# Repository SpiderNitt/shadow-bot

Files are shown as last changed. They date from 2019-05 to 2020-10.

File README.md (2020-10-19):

# Shadow-bot
An all-terrain vehicle with an adaptive suspension that is capable of climbing obstacles (walls).

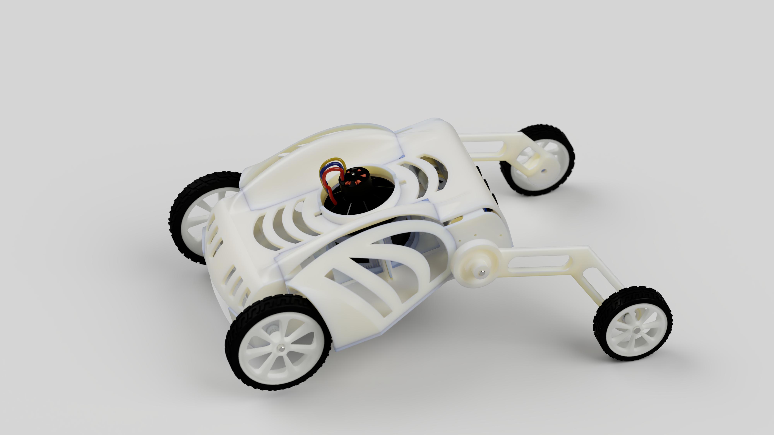
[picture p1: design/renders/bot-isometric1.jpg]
bot


# Research Paper:
[Ibex: A reconfigurable ground vehicle with adaptive terrain navigation capability](https://ieeexplore.ieee.org/document/9196571)

# Team:
  
team

  • Jack Samuel S [https://github.com/jaxxstar] 
  
  • Manu Aatitya [https://github.com/manuaatitya]  
  
  • Senthur Raj [https://github.com/imsenthur]
  
  • Veejay Karthik [https://github.com/vjkarthik97]

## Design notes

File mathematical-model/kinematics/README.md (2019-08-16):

# Longitudinal forward kinematics:

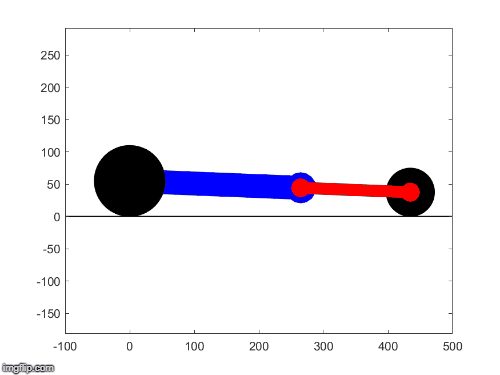
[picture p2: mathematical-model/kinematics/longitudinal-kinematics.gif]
lfk


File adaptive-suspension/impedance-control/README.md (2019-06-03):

# Impedance Control

## Abstract:
The impedance of a mechanical system can be defined as the ratio of the force applied at a point to the resulting velocity at that point. Thus, impedance control is distinct from both position/velocity control and force control. Impedance control is implemented here to achieve the specified desired dynamics.
## Proposed controller
The designed controller is capable of imposing the desired behavior defined by impedance on the original complicated behavior of the end-effector.
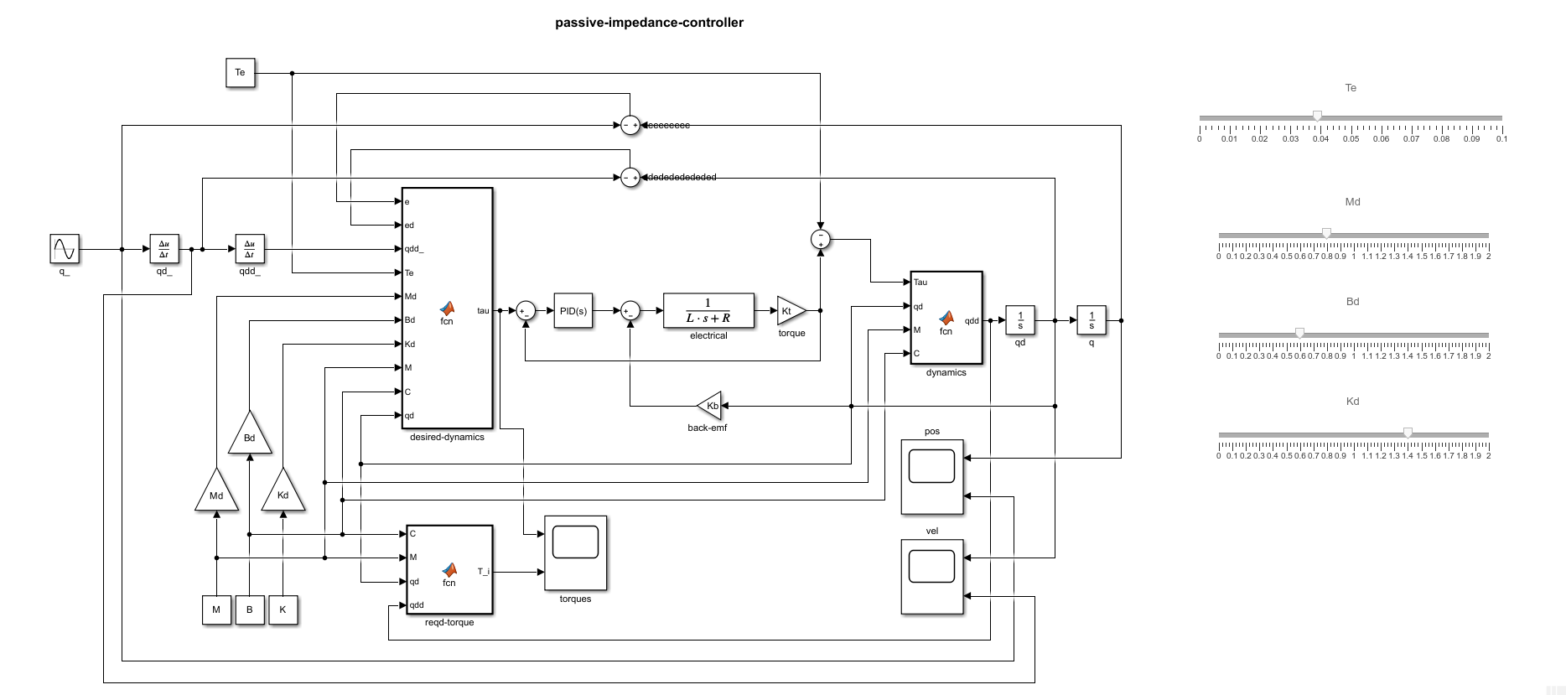
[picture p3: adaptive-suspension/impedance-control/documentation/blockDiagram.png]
Block diagram

## Passivity analysis
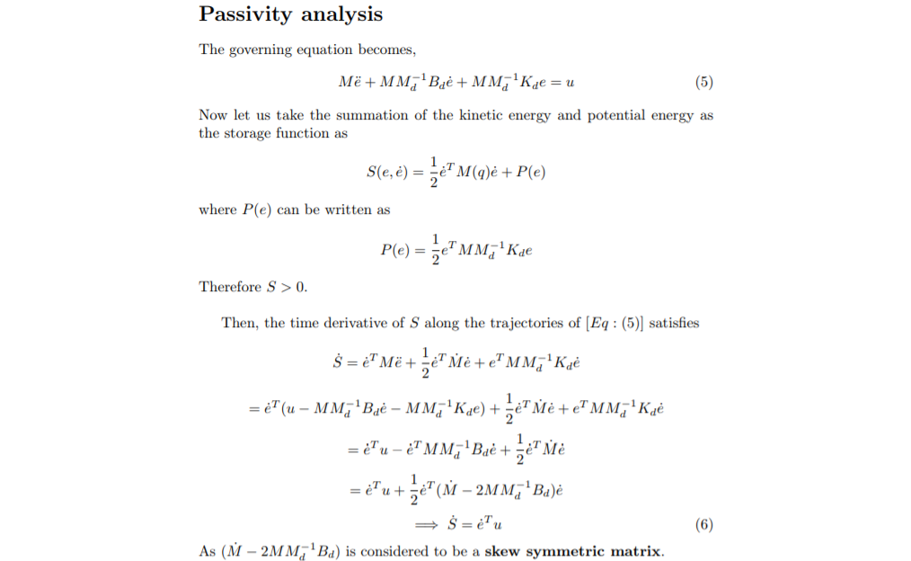
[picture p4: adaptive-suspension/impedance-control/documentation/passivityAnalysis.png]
Passivity analysis

## Modified dynamics
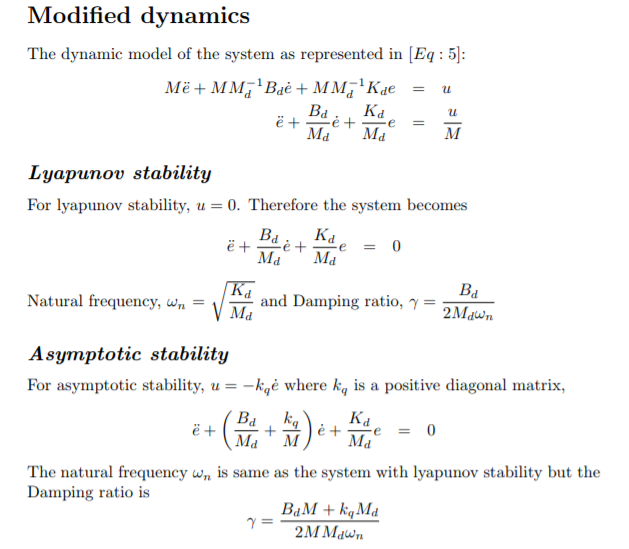
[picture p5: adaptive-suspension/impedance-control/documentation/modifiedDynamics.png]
Modified dynamics

## Results:
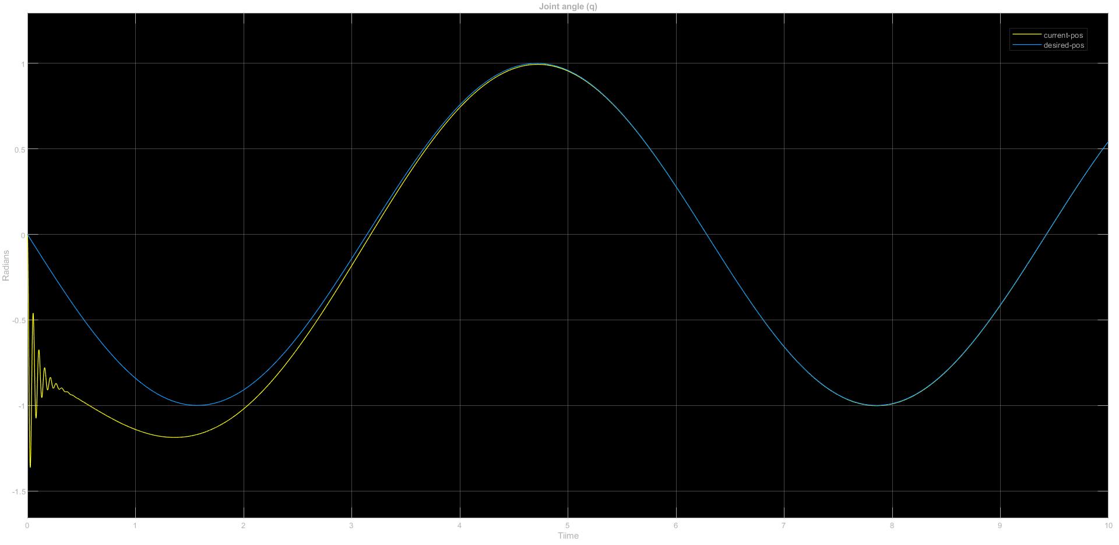
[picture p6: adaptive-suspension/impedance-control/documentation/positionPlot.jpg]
Joint position


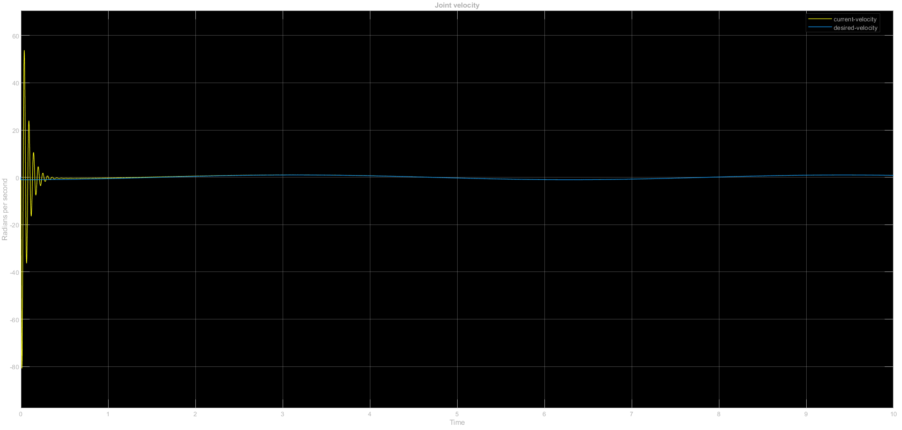
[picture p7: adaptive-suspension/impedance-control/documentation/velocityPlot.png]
Joint velocity


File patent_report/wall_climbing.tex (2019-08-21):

\section{Wall Climbing }
The bot has a unique autonomous wall climbing mechanism which makes it robust to traverse any kind of rough terrain. The wall climbing mechanism is initiated by the response from the ultrasound sensors which detects the presence of obstacles.

The front links then move up and the bot move moves forward. Once the bot reaches the an optimal distance from the obstacle the EDF is turned on to give an upward push and the bot slides along the wall like a ladder. Once the bot is facing the wall the front links are bought down to the original position and the bot moves up on the obstacle due to the EDF Thrust and the rear-wheel drive Torque.

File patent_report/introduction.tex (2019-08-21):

\section{Introduction}

\IEEEPARstart{A}{TR}s  belong to the category of mobile robots which are mainly used for off-road purposes. They usually have wheels or tracks for locomotion. But existing designs have a limitation on the obstacle they can avoid, ie they cannot traverse in a place with really high almost vertical surfaces on all sides. Quite a lot of research has been carried out in the previous decades in this field and excellent ATRs and wall climbing bots have been developed separately.

In the existing Wall climbing bots, an external help is need in order to initially make them fixed to the wall. Several approaches have developed to make the bots move on the walls. Primitive designs use pneumatic suction caps at the end of the actuators to make them fixed on the walls. If the surface is made of ferro-magnetic materials then an electromagnetic actuator is used which gets attached and detached from the surface as the magnet is energized and de-energized. One of the recent bots developed by MIT uses \textit{bio-mimicry} inspired by \textit{Geckos} which have hair like protrusions in order to better grip the surface. But this surface alterations usually involves a cost as nano-materials have to embedded on them. Thus existing bots have a difficulty in commercialization and developed into a product.

Conventional suspensions involve a lot of mechanical components like springs, dampers and struts. The problem with such a system is that a spring has a fixed spring constant and damping constant value arising due to physical structure and material of the spring components. Thus the dynamics of such a system cannot be varied except that a threshold can be set on the maximum load on the spring. Such a spring system cannot be used in an ATR as it encounters new situations depending on the environment it is subjected to. Variable stiffness suspensions are available in the market, but they are expensive and also provide a range of working loads. As loads increase the cost also increase exponentially.

Until recently no bot have been developed with the ability to perform a ground to wall transition autonomously  except \textit{Vertigo}, a bot jointly designed by researchers at \textit{ETH Zurich} and \textit{Disney Research}. Vertigo uses 2 tiltable propellers to maneuver itself in the ground and walls. It has a full carbon fibre frame and servo actuators to rotate the propellers. The carbon fibre frame makes it costly and it also suffers from \textit{gyroscopic precession} which gives a slight jerk whenever the bot tries to change its direction.

The goal of this project is to design an ATR which can be used in any kind of rough terrain with variable size obstacle negotiation capability and dynamic environment adaptability without comprising on the stability at all times. The bot design has been discussed in detail in section II.The Dynamic Analysis, Wall climbing and Adaptive Suspension are discussed in Sections III, IV and V respectively.

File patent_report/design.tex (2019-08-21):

\section{ATR Design}
\begin{figure}
  \begin{center}
  \\
  \caption{Top View of the the proposed design}\label{top_view}
  \end{center}
\end{figure}
The proposed bot design has a set of 2 independently actuated front links who dynamic behaviour can be altered and a set of differential drive rear wheels. Both the rear wheels and the front link positions are actuated using an encoder DC motor. An (Electrically Ducted Fan) EDF is placed in the centre of the bot which provides the necessary thrust during wall climbing to counteract the weight of the bot and provides a kind of drag reduction system during ground motion, aerodynamically aiding the bot's motion in that direction.

%-------------------------------
%   Side View of the bot
%------------------------------

\begin{figure}
  \begin{center}
  \\
  \caption{Side View of the the proposed design}\label{side_view}
  \end{center}
\end{figure}

Slits are cutout from the side of the bot in order to reduce the weight and also to provide an air cooling to the electrical components within the bot. The motors are repeated energizing and de-energizing using an impulse of current in the order of 1 or 2 amperes and over time the current heats the motors due to Joule's Heating Effect and thus needs to be cooled.

Provisions for ultrasound distance sensors and camera are provided in the front of the bot. The cameras help in sensing the environment and relaying the obtained data to a remote location through the on-board WiFi module. The ultrasound sensors help in detecting obstacles, if any, in the advancing direction and the on-board computer sends the appropriate signals to actuate the front links and avoid it.

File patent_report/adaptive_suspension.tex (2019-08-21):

\section{Adaptive Suspension}
Adaptive suspension is one of the key features of shadow bot. The dynamics of the front links can be altered to that of any spring constant and damping constant value thus making it behave as if different springs are being for suspension depending in the load.

Initially the front links are set a desired position. Whenever it encounters an impact the position deviates from the set-point. This change is sensed by the encoders in the motors and error(change in the position) is computed. An impulse of current is sent to the motor which produces a counter torque to balance the impact. Since the frequency of the clock on the on-board CPU is 8MHz, it takes utmost a few milliseconds to react without any delay as electrical components actuate the link whereas in conventional suspensions a lot of delay (on the timescale of electrical actuation) is introduced due to the presence of mechanical and fluid elements in the system.

\begin{figure}[h]
  \begin{center}
  
  \caption{Dynamic behaviour of the link to a varying input}\label{suspesnion_graph}
  \end{center}
\end{figure}

Figure~\ref{suspesnion_graph} shows the response of the link to a varying input. The rise in displacement is the disturbance created from the set position and the fall of displacement is the system's response to the situation. It is observed that the system tries to establish equilibrium is quickier than the time taken to cause the disturbance.

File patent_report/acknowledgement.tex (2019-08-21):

\section*{Acknowledgment}

%Dr. Reveryrand would like to acknowledge the funding by XLIM, Limoges, France. 
We would like to thank the admin, NIT Trichy for providing us a waiver on the 3D printing Cost of the prototype and Siemens COE in Manufacturing, NIT Trichy for 3D Printing the prototy

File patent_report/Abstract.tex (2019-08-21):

\begin{abstract}
%\boldmath

This paper presents the design and dynamical analysis of an All Terrain Robot (ATR) with a novel suspension and wall climbing mechanism. One of the main subsystems of an ATR is the suspension. Traditional suspensions involve spring and dampers with fixed properties which limit the usability of the vehicle. The proposed design uses a rigid front link whose dynamics can be altered according to the impact, thus providing stability in a wide range of environmental conditions. One of the main limitations of the existing all terrain bots is wall climbing. The front links in the proposed design uses a unique wall climbing mechanism to move from the ground to the walls autonomously, which most of the existing design do not address to.

\end{abstract}

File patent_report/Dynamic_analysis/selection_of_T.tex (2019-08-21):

\subsection {Selection of \textbf{T} and \textbf{M_{r}}} 

Consider the bot as shown in Fig.~\ref{top_view}. Let the thrust force provided by the EDF be $\textbf{T}$ \textit{kgf} and the mass of the bot be $\textbf{W}$ \textit{kgf}. When the bot is trying to climb a wall of average coefficient of kinetic friction $\mu$, the following conditions should be satisfied,\\
For No Sliding in the Wall Surface,
\begin{equation}\label{no_sliding}
T \geq \frac{W}{\mu}
\end{equation}

And for No Toppling from the Wall Surface,
\begin{equation}\label{no_toppling}
W \leq T * \frac{x}{c}
\end{equation}
where \textbf{x} is the distance of the EDF centre from the rear wheel of the bot and \\
\textbf{c} is the clearance of the bot with the ground.\\

The required motor torque, \textbf{$M_r$} for the rear wheels to remain in contact with the wall at all times is 
\begin{equation}\label{motor_torque}
M_r \geq \frac{W*R}{2}
\end{equation}
where \textbf{R} is the radius of the wheel.\\

Since we have a range of Thrust, \textbf{T} and Motor torque, \textbf{$M_r$} values to choose from, it must be ensured that the following conditions are always met for the bot to be able to climb on walls,

\begin{equation}\label{thrust_check}
T \geq \frac{W*c - M_r}{x}
\end{equation}

In order to choose the required \textbf{T} and \textbf{W}, the following plots were made :

\begin{figure}[h]
  \begin{center}
  \\
  \caption{T vs W plots for different $\frac{x}{c}$ ratios}\label{TvsW}
  \end{center}
\end{figure}

From Fig.~\ref{TvsW} it is evident that the maximum \textbf{W} that can be lifted for a given value of \textbf{T} is obtained when the EDF is placed at \textit{twice} the clearance of the bot, from the rear end.

\begin{figure}[h]
  \begin{center}
  \\
  \caption{T vs $M_r$ plots for different $\frac{x}{c}$ ratios}\label{TvsTorque}
  \end{center}
\end{figure}

From Fig.~\ref{TvsTorque} it can be inferred that for a given \textbf{T}, \textbf{$M_r$} required to maintain the bot's contact is maximum at \textit{twice} the clearance of the bot, from the rear end.

Thus from the plots it can be concluded that :
\begin{itemize}
    \item There is a trade-off between the payload capacity of the bot and Motor torques for a given amount of Thrust. This can be varied to suit the bot's application, ie for defense applications weight cannot be compromised whereas for inspection in chimneys bot weight can be reduced and thus reducing the cost of the bot.
    \item The $W_{min}$ of the bot that the thrust can support depends on $\mu$ and \textbf{T} only and is independent of other parameters.
    \begin{equation}
        W_{min} = \mu * T
    \end{equation}
\end{itemize}

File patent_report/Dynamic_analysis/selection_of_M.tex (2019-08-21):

\subsection {Selection of \textbf{$M_f$}}

Since front links also share the load of the bot, the minimum torque required to actuate the front links,$M_f$ against the inertial forces must also be analyzed.

\begin{figure}[h]
  \begin{center}
  \\
  \caption{Orientation of the bot in a given state}\label{front_links}
  \end{center}
\end{figure}

Consider a bot orientation as shown in the figure.
Analysing the bot using the method of \textbf{virtual work} to obtain the min Motor torque required we get,\\
Let the distance of the center of mass of the bot from the rear wheels be \textbf{x} and the length of the front links be \textbf{L}.\\
Let's say that the motor produces a torque,$M_f$  to actuate the front wheels,\\
The work done by the motor to rotate the link by an angle $d\theta$ is $M_f * d\theta$.\\
To find Work done by gravity :\\
Using sine rule in the triangle ABC we get,

\begin{equation}\label{sine_rule}
    \frac{sin(\theta}{x} = \frac{sin(\alpha)}{L}
\end{equation}

let the height of the centre of mass of the bot from the ground be \textbf{h},

\begin{equation}
    h = x * sin(\alpha)
\end{equation}

but from equation~\ref{sine_rule}, we get,
\begin{equation}
    x * sin(\alpha) = L * sin(\theta)
\end{equation}
Relating the unknown variables in terms of the known variables using the above equations,  
Work done by gravity for a small displacement $d\theta$ is $-W * x \ *cos(\theta) * d\theta$,\\
the minus sign indicates that the gravity does negative work.\\
Work done by the normal reactions $N_1 \ and \ N_2 \ is \ 0$, since there is not net displacement in the vertical direction.\\
But Frictional force $Fr_{2}$, does some work.\\
let the distance of the front wheel from the point of connection of the front links be y then,\\
$y \ = \ x * cos(\theta)$\\
Work done by frictional force  = $Fr_{2} * x * sin(\theta)*d\theta$\\
Now using work energy theorem we get,\\ $W_{net} \ = \Delta KE_{system}$,
 but since the system is at rest,  
$ KE_{system} \ = \ 0 $
and we get,\\
$ -W * \ x  * \ cos(\theta) * \ d\theta \ + \ Fr_{2} \ * \ x \ * \ sin(\theta)* \ d\theta \ + \ M_{f} * \ d\theta \ = \ 0 $.

Thus $M_{f} \ = W \ * \ x  * \ cos(\theta) * \ d\theta \ - \ Fr_{2} \ * \ x \ * \ sin(\theta)* \ d\theta$,

At $\theta = 0 ^ o$,\\ \\
$M_{f} \ = \frac{W*L*l}{x}$,\\ \\
which is the minimum Motor Torque required for the front links to be actuated.

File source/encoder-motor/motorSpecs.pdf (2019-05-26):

## SPG

## 30 Series

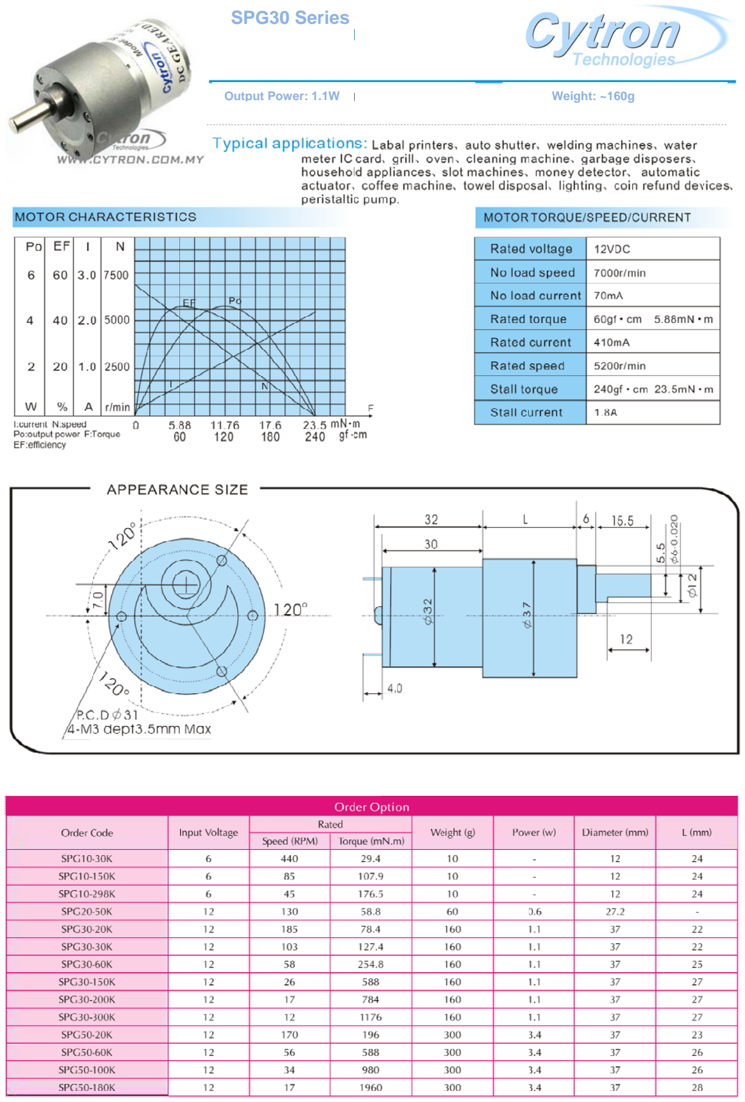
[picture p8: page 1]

Output

Power: 1.1W | Weight: ~160g

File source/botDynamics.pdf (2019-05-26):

## Shadow Bot Calculations

The governing equations are :
Let the Thrust supplied by the EDF be T, and the Weight off the bot be W, then for No Sliding,

and for No Toppling,

where,
x is the point of application of thrust from the rear wheel of the bot, c is the clearance of the bot with the ground.
For the bot to move ,
Motor torque,M required is ,

where,
R = radius of the wheel.

And also the bot should satisfy these conditions while running,

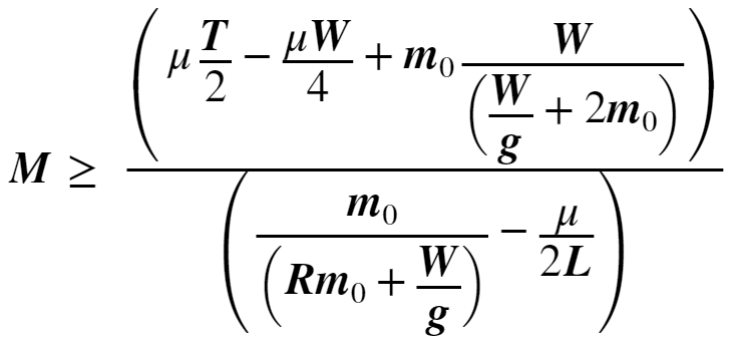
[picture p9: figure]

which has to ensured.
Thrust vs W_max of the bot calculation for different Thrust_distance(x)/clearance of bot ratios keeping other parameters fixed :

% Thrust vs W_max of the bot calculation for different % Thrust_distance(x)/clearance of bot ratios keeping % other parameters fixed
x = table2array(TvsM(13:27,2));
y = table2array(TvsM(13:27,10));
x1 = table2array(TvsM(28:42,2)); y1 = table2array(TvsM(28:42,10)); x2 = table2array(TvsM(43:57,2)); y2 = table2array(TvsM(43:57,10)); x3 = table2array(TvsM(58:72,2)); y3 = table2array(TvsM(58:72,10)); figure;
hold on;
xlabel('Thrust');
ylabel('W-max-toppling');
title('T vs W-max');
plot(x,y,x1,y1,x2,y2,x3,y3);
legend('x/c = 10/8','x/c = 10/7','x/c = 10/6','x/c = 10/5'); grid on;
hold off;

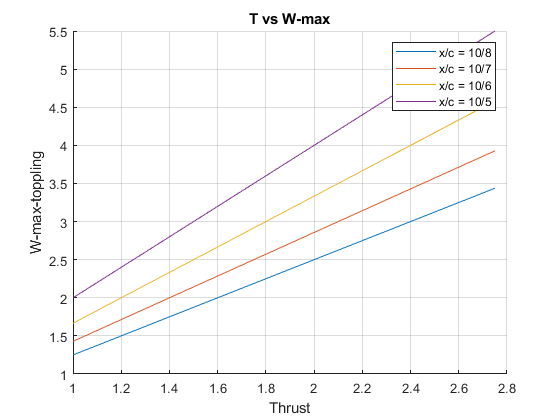
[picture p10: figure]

Motor Torque vs Thrust for the same above conditions :

% Motor Torque vs Thrust for the same above conditions z = table2array(TvsM(13:27,12));

z1 = table2array(TvsM(28:42,12)); z2 = table2array(TvsM(43:57,12)); z3 = table2array(TvsM(58:72,12)); figure;
hold on;
xlabel('Thrust');
ylabel('Motor-Torque-max');
title('T vs Motor-Torque-max'); plot(x,z,x1,z1,x2,z2,x3,z3);
legend('x/c = 10/8','x/c = 10/7','x/c = 10/6','x/c = 10/5'); grid on;
hold off;

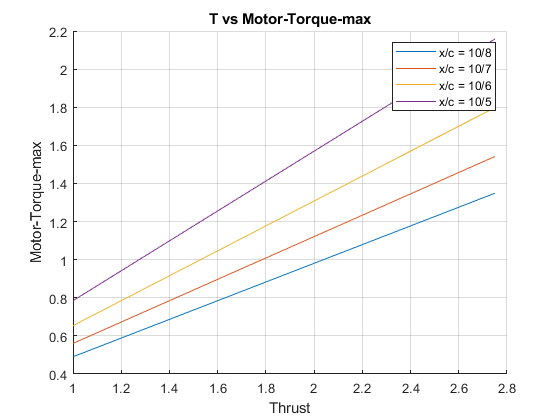
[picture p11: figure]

The Min Motor Torque ,

and | = | and hence depends on µ and T only. It does not depend on other parameters.

Front Wheel Motor Torque:

Calculations for the minimum motor torque required to actuate the front links :

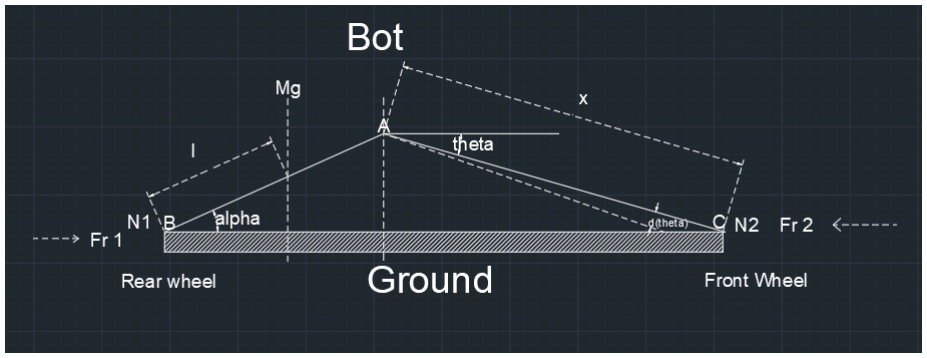
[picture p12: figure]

Analysing the bot using the method of virtual work to obtain the min Motor torque required we get, Le the distance of the center of mass of the bot from the rear wheels be l,
the length of the front links be x.
Let's say that the motor produces a torque, | to actuate the front wheels,
the Work done by the motor to rotate the link by an angle | =

To find Work done by gravity :
Using sine rule in the triangle ABC we get,

let the height of the centre of mass of the bot from the ground be h,

but from (1) we get

but | , where

distance of COM from the back link along the back link

Removing the unknown variable y and relating l and L with the height we get ,

and therefore,

so

Work done by gravity during this time = - | ,

the minus sign indicates that the gravity does negative work.

Work done by the normal reactions | , since there is not net displacement in the vertical direction.

But , frictional force does some work

let the distance of the front wheel from the point of connection of the front links be y then,

Work done by frictional force =

Now using work energy theorem we get ,

Work done by net forces , | but since the system is at rest ,

= 0

and we get ,

- | + ( | ) + | = 0
= | -
and at | we get ,

=

which is the minimum Motor Torque required by the front wheels to be actuated.

Wheel Design :

Euler characteristic ( of Wheel (Disc) is 1.

But,

where,

V is the number of vertices, E is the number of edges,
F is the number of faces.
Let the disc contain P number of Pentagons, H number of Hexagons,
then,

Substituting these values we get,

But we need to find the number of Hexagons,
The number of Hexagons can be arbitrary to fill the remaining space, Here I needded 5 hexagons to cover the fill the disk.
So for our case,

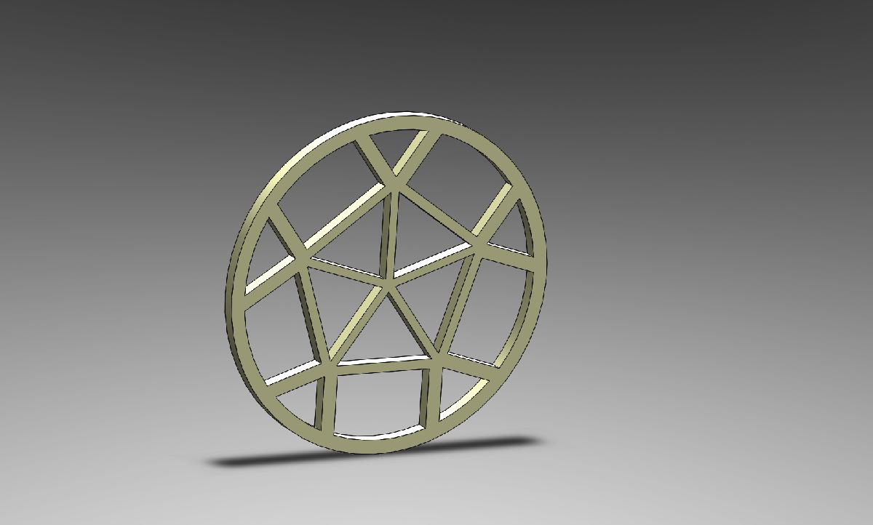
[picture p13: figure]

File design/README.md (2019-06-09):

# Design and development of shadow-bot

## Renders:
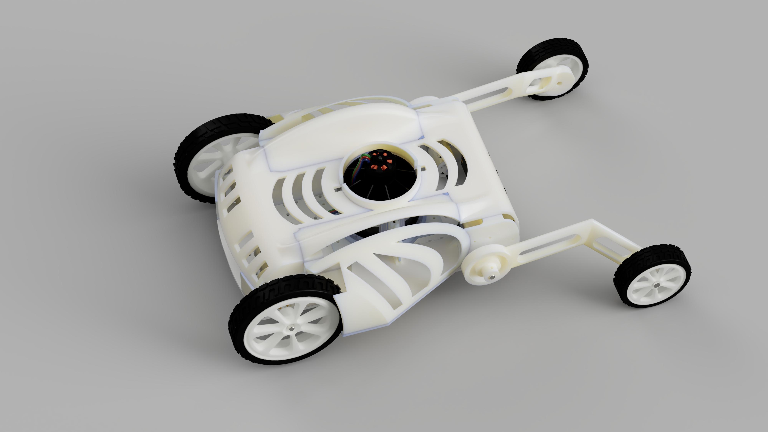
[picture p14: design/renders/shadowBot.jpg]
Passivity analysis


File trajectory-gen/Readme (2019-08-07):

pso1.m - Main Program,run this!!
PSO.m - The Algorithm
conv_splineg1.m - finds and returns the spline characteristics
Sphere.m - The Cost Function

The Trajectory Generated by this is given to the controller as a the reference to be followed.

In this problem we try to generate trajectories based on cubic
splines.The cubic splines require a set of waypoints and a set of time
stamps during which they have to be traversed through.The waypoints are
generated from path planning algorithms and the time stamps are to
determined based on the physical limitations of acceleration and
velocities of our bot.This trajectory generation aims to generate a set of optimal time intervals which 
helps us to construct the required cubic
spline.Since the optimization problem here is highly non convex and non
linear in case of cubic splines,we employ a method called particle swarm optimization to help us
achieve our objective.

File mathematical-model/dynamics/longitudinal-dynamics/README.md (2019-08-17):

# Longitudinal Dynamics:

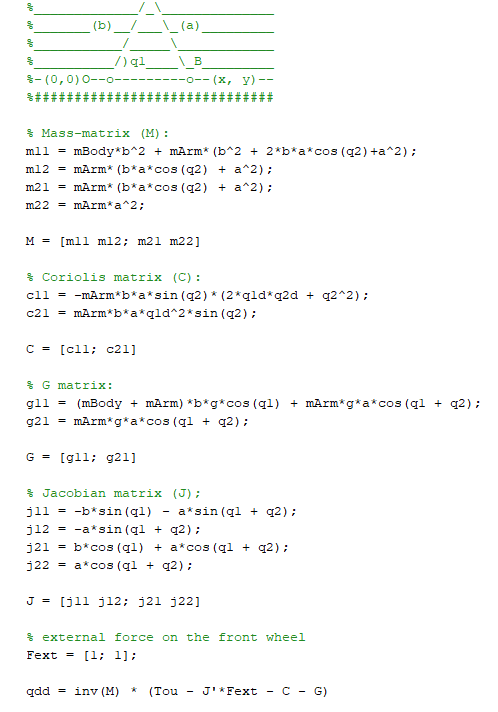
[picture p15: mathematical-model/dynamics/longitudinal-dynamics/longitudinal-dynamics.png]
LD


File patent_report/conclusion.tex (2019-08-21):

\section{Conclusion}
In summary, this report discusses about :
\begin{itemize}
    \item ATRs and wall climbing bots, the existing designs and limitations,
    \item How the proposed design overcomes the limitations presented by the existing bots, without compromising the performance,
    \item How adaptive suspension is superior to the current technologies for suspensions in ATRs or All Terrain Vehicles in general,
    \item How the integration of the suspension and wall climbing modules makes the bot traverse through any terrain with ease and
    \item How the cost of maintenance and repair in conventional ATRs can be reduced by introducing the proposed modules.
\end{itemize}

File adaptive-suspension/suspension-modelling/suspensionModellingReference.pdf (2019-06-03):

Modelling:

Models can be based on equation, data.

Different types of modelling using Simulink:

i) Mathematical Models (Writing equations)

1.First Principles

2.Component-based physical models

ii) Black Box Models (Solely based on input and output data)

1.Lookup Tables

2.System Identification *(Dynamically changing functions using curve fitting)

iii)Grey Box Models (We know some eqns. but not sure about the parameters so we write eqns. and collect data so that the data can be used to tune the parameters)

1.Parameter estimation*

*Powerful tools

Models can be generally divided into 2 parts:

i) Plant Model- Virtual Prototype of a real physical System and these systems can be modelled with the help of data collected from the real system (or) getting the mathematical equation from physics

ii) Algorithm- Control and Logic systems, Design in Simulink and then generate code for the embedded system

Simulink helps us to combine these 2 parts

Suspension System of Cars:

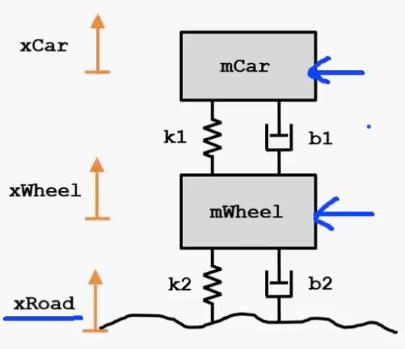
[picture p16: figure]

There is assumed to be one extra set of spring and damper one between the wheel and the road and the other which is physically present

This is done in real cars because to account for the wheel squishing against the road, but we can choose to neglect this in shadow bot

## Mathematical Modelling of Car suspension:

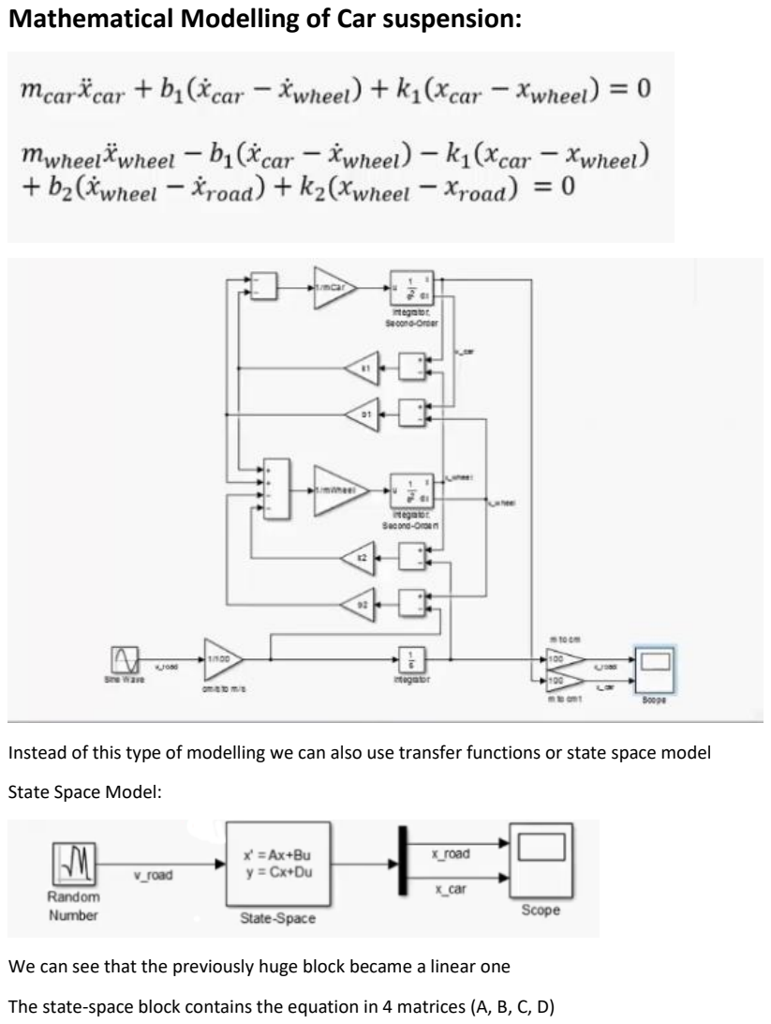
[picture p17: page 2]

Instead of this type of modelling we can also use transfer functions or state space model

State Space Model:

We can see that the previously huge block became a linear one

The state-space block contains the equation in 4 matrices (A, B, C, D)

Component Based Modelling (Simscape):

Simscape a tool for physical modelling which has blocks which has the equations inside it i.e. we don’t need to know the equations and if there are any changes in the system then we don’t need to re formulate the eqns. again from scratch we can just alter the blocks

Both Simulink and Simscape are compatible i.e. we can integrate plant model in Simscape and control in Simulink with the help of interface blocks

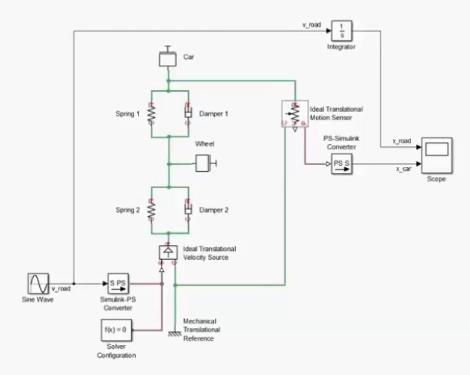
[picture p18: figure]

Black Box Approach:

We have this data:

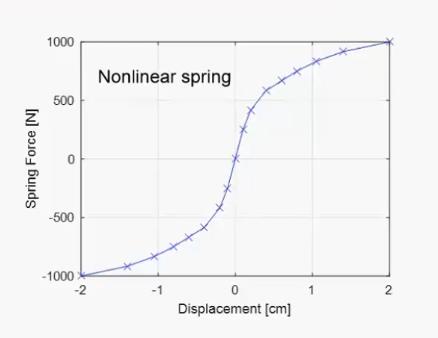
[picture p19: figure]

We can import data from excel sheets or text file

We simply insert a block stating the parameters from the file which has the plots

Parameter Estimation:

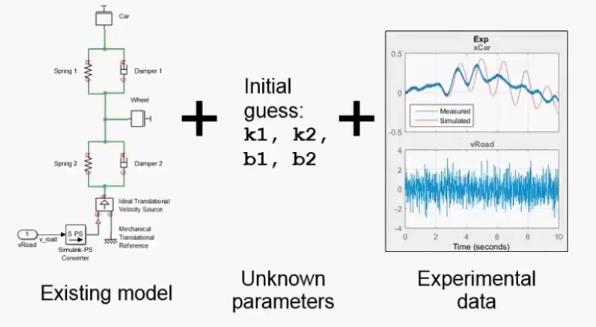
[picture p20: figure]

In this method if it takes too long for the computer to iterate and simulate the data we could something called as parallel computing &|| GPU computing which would be really cool.

Here the parameters are given an initial guess and MATLAB iterates the simulation many number of times to get an optimised value for those parameters (We will have to read about optimisation theory)

System Identification:

This type of modelling is done when we don’t know anything about the system except for input and output data

Here we could really play around with MATLAB and write different Model structures such as state space/ transfer function/ Non-linear model, but for a particular system a particular model structure will work flawlessly, so we’ll have to decide which structure we are going to use in case we are going to use system identification modelling.

To get the best model structure we start with the simpler linear model (State Space) and if it does not work fine then we go to transfer function or non-linear structure

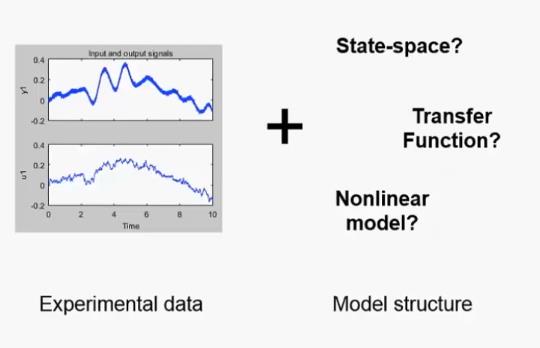
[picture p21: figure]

System Identification by state space approach:

By using state space model, we could know the different states of the system at any instant

Here we specify the order of the system, i.e. the number of system variables

Guidelines for choosing from the different model approach

1.How much we know about the model (Physics of the model)

If we know everything then we could use the mathematical approach in which the model will be the most accurate to real world, but In case we don’t know anything about the model it is okay to use system identification approach

2.How much detail we want from the model.

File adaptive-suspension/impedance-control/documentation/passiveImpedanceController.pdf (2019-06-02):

# Impedance controller and design of desired parameters

Senthur Raj

May 30, 2019

## Introduction

This report describes the way of approach, the progress and the results obtained. The research objective is to find a novel way to design the impedance parameters (Md, Bd and Kd) with the help of passivity analysis.

## Passivity

Let us consider a system H with input u(t) and output y(t), where H is regarded as a mapping from input space to output space. Then, passivity of the map can be defined as [1],
The system H : u =⇒ y is said to be passive if there exists a positive constant β such that,
Z τ

0

y

T
(t)u(t)dt ≥ −β

for all input signals u(t) and for all τ ∈ R⁺. In addition, H is said to be

- Input strictly passive if there exists a positive scalar δu such that
Z τ

0

y

T
(t)u(t)dt ≥ −β + δu

Z τ

0

||u(t)||²
dt,
- Output strictly passive if there exists a positive scalar δy such that
Z τ

0

y

T
(t)u(t)dt ≥ −β + δy

Z τ

0

||y(t)||²
dt,

For example, let us consider a n-link manipulator, the robot dynamics can be written as
M(q)¨q + C(q, q˙) ˙q + G(q) = T | (1)

1

where q, ˙q and ¨q represent joint angles, velocities, and accelerations respectively, and T represents the input torque vector. The matrices M(q) and C(q, q˙) represent the manipulator inertia matrix and Coriolis matrix respectively and the gravity vector G(q) can be written as

G(q) =
∂P(q)

∂q T

where P(q) is potential energy of the system.
It is well known that M(q) is positive definite and the matrix

M˙
(q) − 2C(q, q˙)

is skew-symmetric by defining C(q, q˙) using the Christoffel symbols.
Let us take the summation of the kinetic energy and potential energy as the storage function as
S(q, q˙) = 1
2

q˙

TM(q) ˙q + P(q)

Then, the time derivative of S along the trajectories of Eq : (1) satisfies

S˙ = ˙q
TM(q)¨q +
1/2 q˙

TM˙
(q) ˙q +
∂P (q)

∂q
q˙

= ˙q

T

(T − C(q, q˙ − G(q)) + 1
2

q˙

TM˙
(q) ˙q + G(q)

T
q˙)

= ˙q

T T −
1/2 q˙

T

(M˙
(q) − 2C(q, q˙)) ˙q

=⇒ S˙ = ˙q
T T

The last equation holds because of the skew symmetry of M˙
(q)−2C(q, q˙). This
means passivity of the manipulator dynamics from the input torque T to the joint velocity ˙q.

## Impedance control

The designed controller is capable of imposing the desired behavior defined by impedance on the original complicated behavior of the end-effector [2]. The actual dynamic model of a 5-bar manipulator can be expressed as

M(q)¨q + C(q, q˙) ˙q + G(q) = Tinp − Text | (2)

The desired impedance model according to the specific work requirements which is usually specified as a second-order dynamic equation:

Mdë+ Bde˙ + Kde = −Text | (3)

where e = (q − qd).

2

After substituting the target impedance [Eq : 3] into the actual manipulator dynamics [Eq : 2] by eliminating ¨q, a specific control law is obtained as

Tinp = u+(1+MM⁻¹
d

)Text+C(q, q˙) ˙q+G(q)+M(q)[ ¨qd−M⁻¹
d

[Bde˙+Kde+Text]]
(4)
since
q¨ = ¨qd − M⁻¹
d

[Bde˙ + kde + Text]

The control law [Eq : 4] is the desired one to make the actuators produce torque Tinp. Then the manipulator driven by Tinp will perform the behavior defined by impedance in [Eq : 3].

## Passivity analysis

The governing equation becomes,

Më+ MM⁻¹

d | Bde˙ + MM⁻¹
d | Kde = u | (5)

Now let us take the summation of the kinetic energy and potential energy as the storage function as

S(e, e˙) = 1
2

e˙

TM(q) ė + P(e)

where P(e) can be written as

P(e) = 1
2

e

TMM⁻¹
d Kde

Therefore S > 0.

Then, the time derivative of S along the trajectories of [Eq : (5)] satisfies

S˙ = ė
TMë+

1
2

e˙

TM˙ e˙ + e

TMM⁻¹
d Kde˙

= ė

T

(u − MM⁻¹

d | Bde˙ − MM⁻¹
d | Kde) + 1
2 | e˙ TM˙ e˙ + e

TMM⁻¹
d Kde˙

= ė

T u − e˙

TMM⁻¹
d | Bde˙ +
| 1
| 2 e˙ TM˙ e˙

= ė

T u +

1
2

e˙

T

(M˙ − 2MM⁻¹
d Bd) ė

=⇒ S˙ = ė
T u | | (6)

As (M˙ − 2MM⁻¹
d Bd) is considered to be a skew symmetric matrix. [Eq : 6] implies that the system [Eq : 5] is passive from input u to output e˙. Also notice that the storage function is shaped so that it takes the minimal value at e = 0 and ė = 0.

3

Substituting ė = 0 and u = 0 in [Eq : (5)], we get

e = 0

and hence the system is zero-state observable and lyapunov stable. Thus, the damping injection
u = −kqe˙ | (7)

If kq is a diagonal positive gain matrix, then it guarantees
asymptotic stability of the origin ė = 0 and e = 0.

## Modified dynamics

The dynamic model of the system as represented in [Eq : 5]:

Më+ MM⁻¹

d | Bde˙ + MM⁻¹
d | Kde = u

ë+

Bd
Md

e˙ +

Kd
Md

e =

u
M

Lyapunov stability

For lyapunov stability, u = 0. Therefore the system becomes

ë+

Bd
Md

e˙ +

Kd
Md

e = 0

Natural frequency, ωn =

r
Kd
Md

and Damping ratio, γ =

Bd
2Mdωn

Asymptotic stability

For asymptotic stability, u = −kqe˙ where kq is a positive diagonal matrix,

ë+

Bd
Md

+

kq
M
e˙ +

Kd
Md

e = 0

The natural frequency ωn is same as the system with lyapunov stability but the Damping ratio is

γ =

BdM + kqMd
2MMdωn

## References

[1] Takeshi Hatanaka, Nikhil Chopra, Masayuki Fujita, and M.W. Spong. Passivity-Based Control and Estimation in Networked Robotics. 01 2015.
[2] P. Song, Y. Yu, and X. Zhang. Impedance control of robots: An overview. In 2017 2nd International Conference on Cybernetics, Robotics and Control (CRC), pages 51–55, July 2017.

4

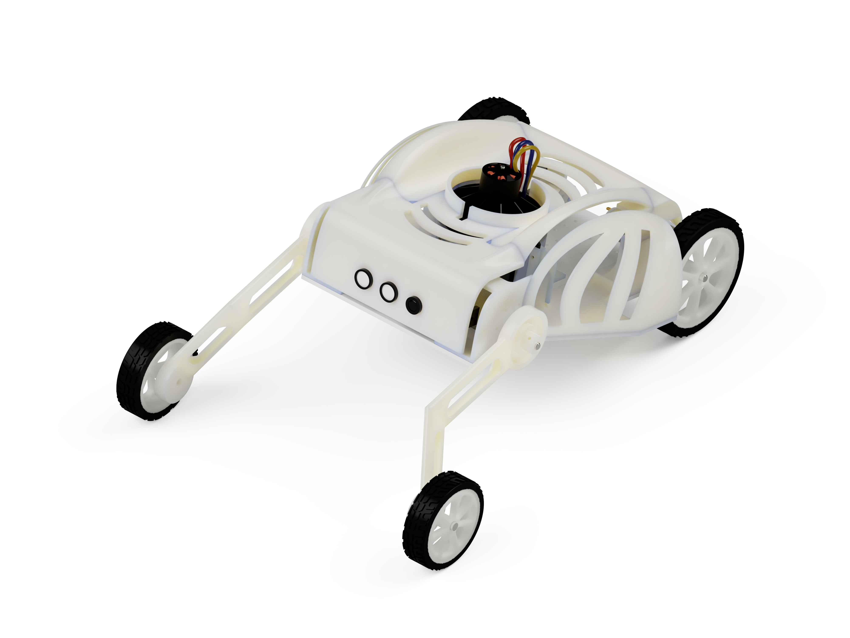
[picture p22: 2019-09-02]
design/renders/ICRA/isometric.PNG

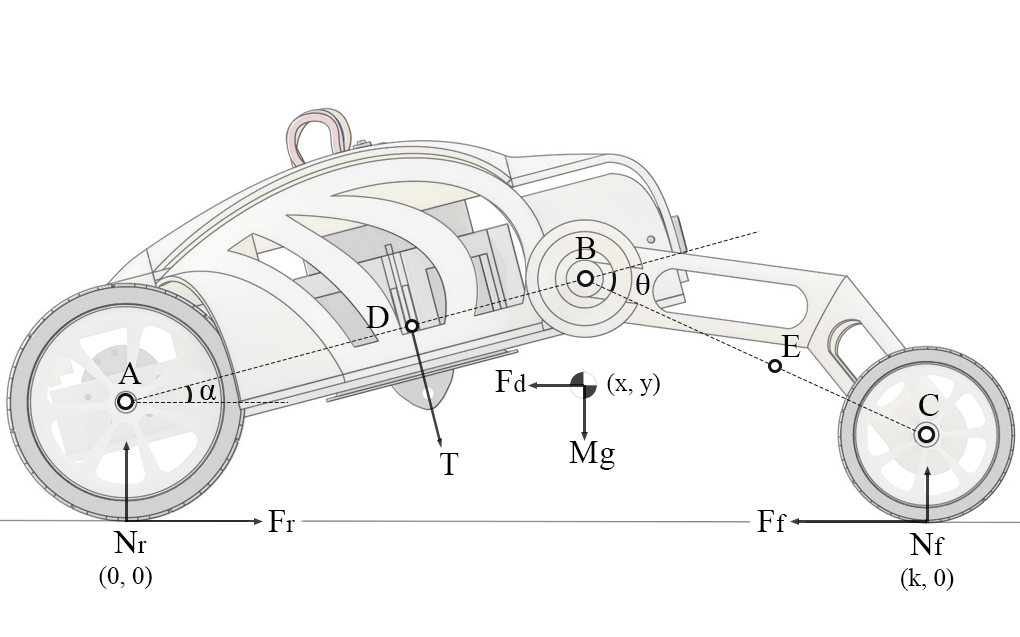
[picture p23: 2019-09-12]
design/renders/ICRA/fbd-kinematics-fusion.png

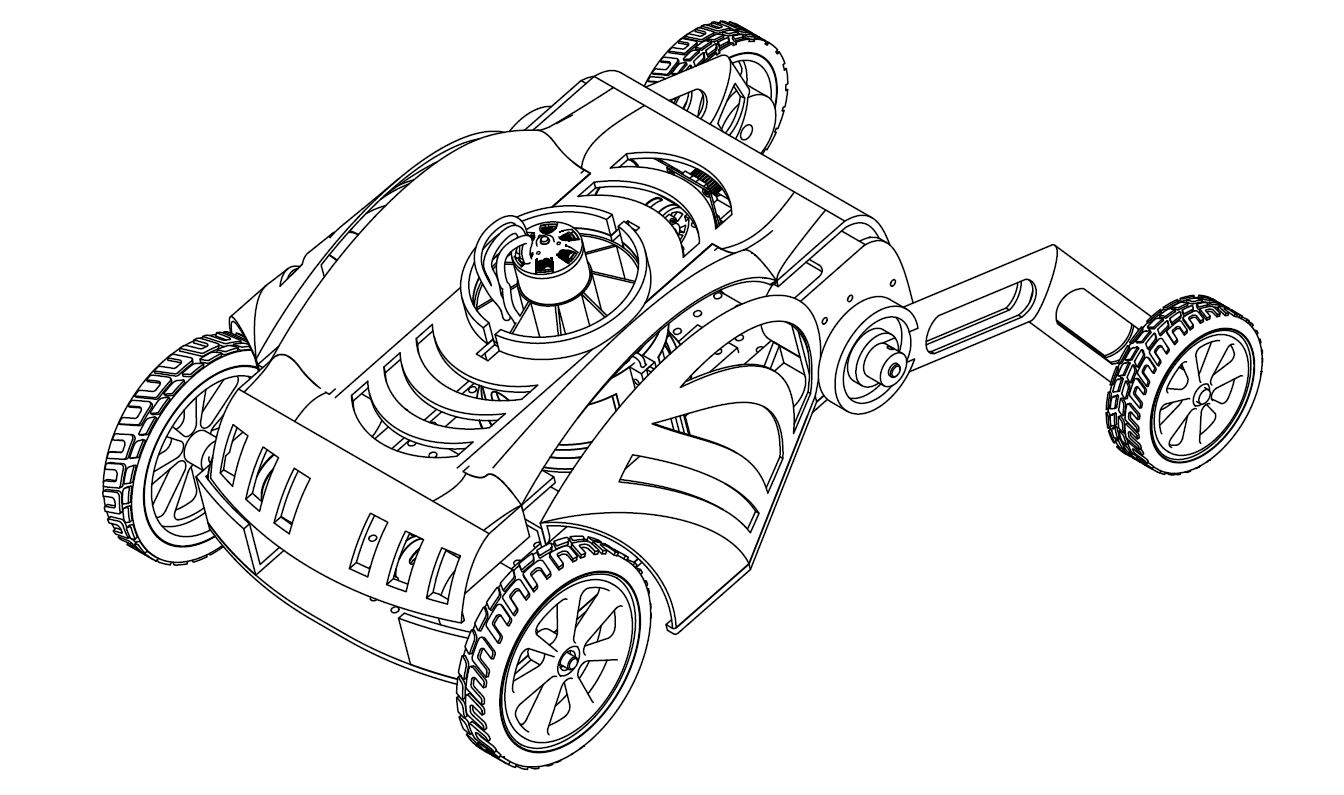
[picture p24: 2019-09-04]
design/renders/ICRA/sw-isometric-drawing.JPG

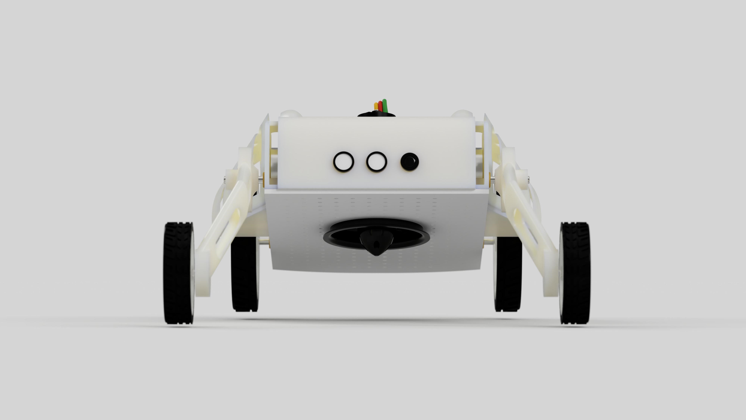
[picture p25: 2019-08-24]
design/renders/front-view.jpg

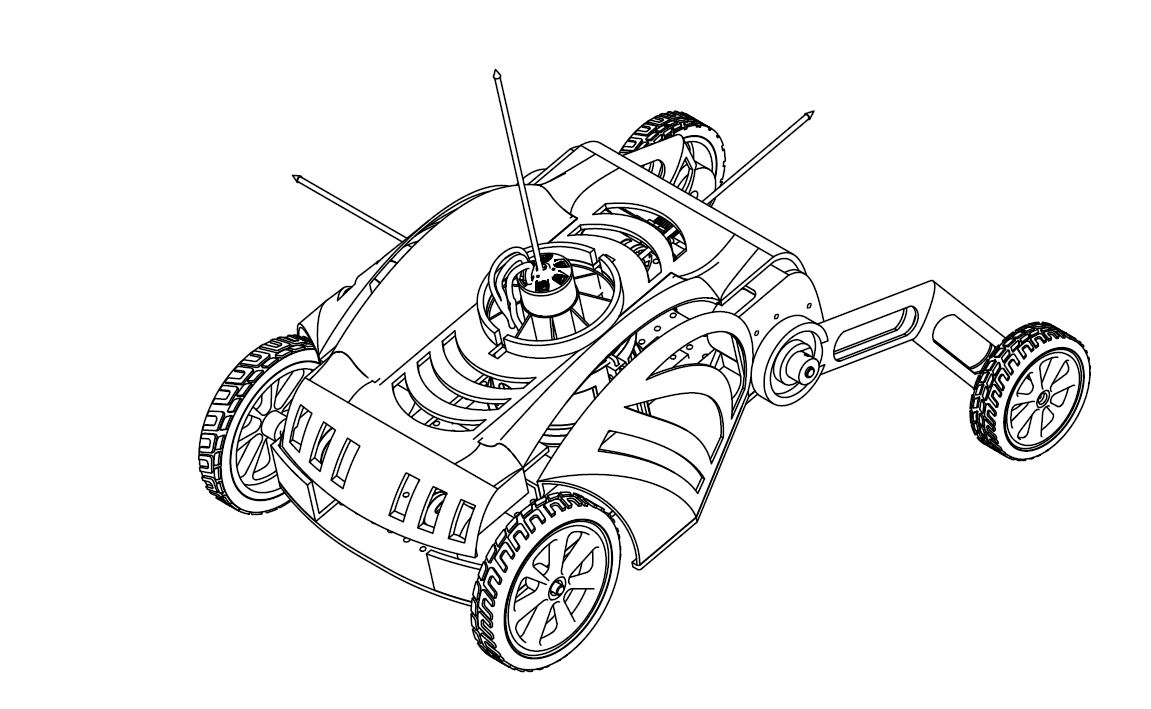
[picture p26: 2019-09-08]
design/renders/ICRA/origin.JPG

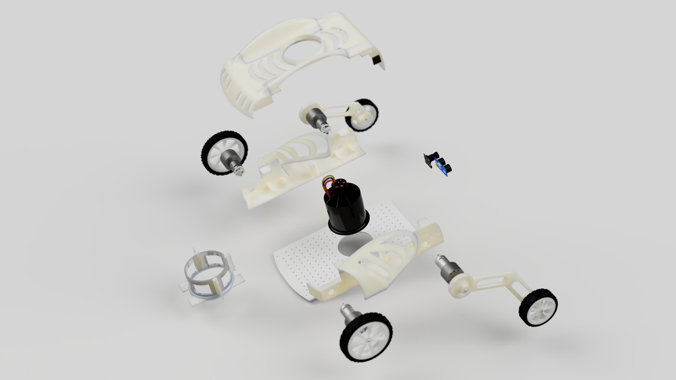
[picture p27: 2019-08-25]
design/renders/bot-exploded-view.jpg

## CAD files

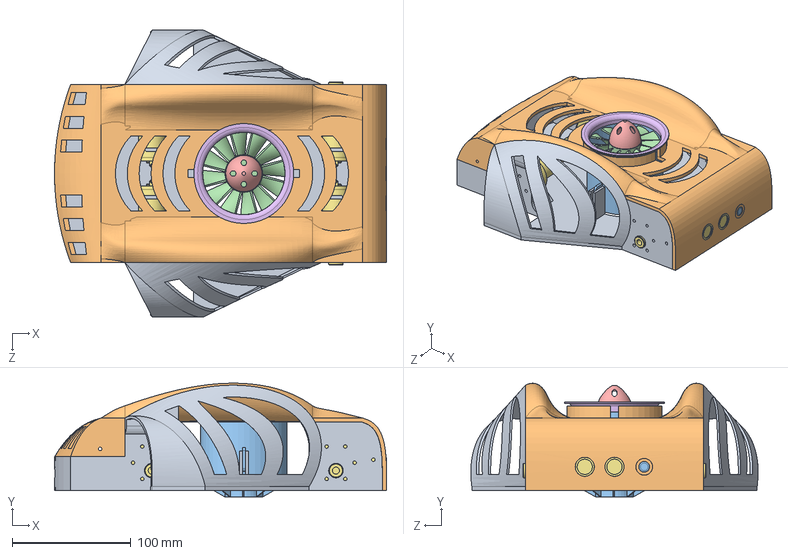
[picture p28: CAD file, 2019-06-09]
design/parts/body.SLDASM
279.2 x 95.6 x 241.7 mm
chassis
surfacePlate
edf_housing
edf_blades
edf_wiresNose
edf_rim
urFinder
PCB 1
Camera Block
Camera end
Lenz
15 Pin Ribbon Block
Ribbon Clamp
0603 Resistor x 4
motor x 4

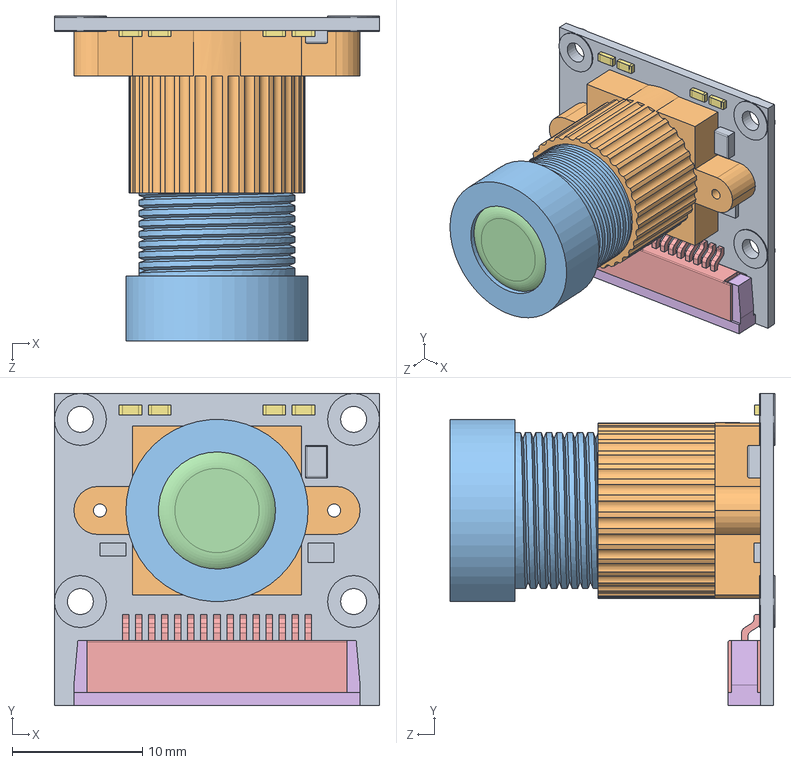
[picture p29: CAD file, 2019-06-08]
design/parts/piCam/Camera Module Assem.SLDASM
25.0 x 24.0 x 25.0 mm
PCB 1
Camera Block
Camera end
Lenz
15 Pin Ribbon Block
Ribbon Clamp
0603 Resistor x 4

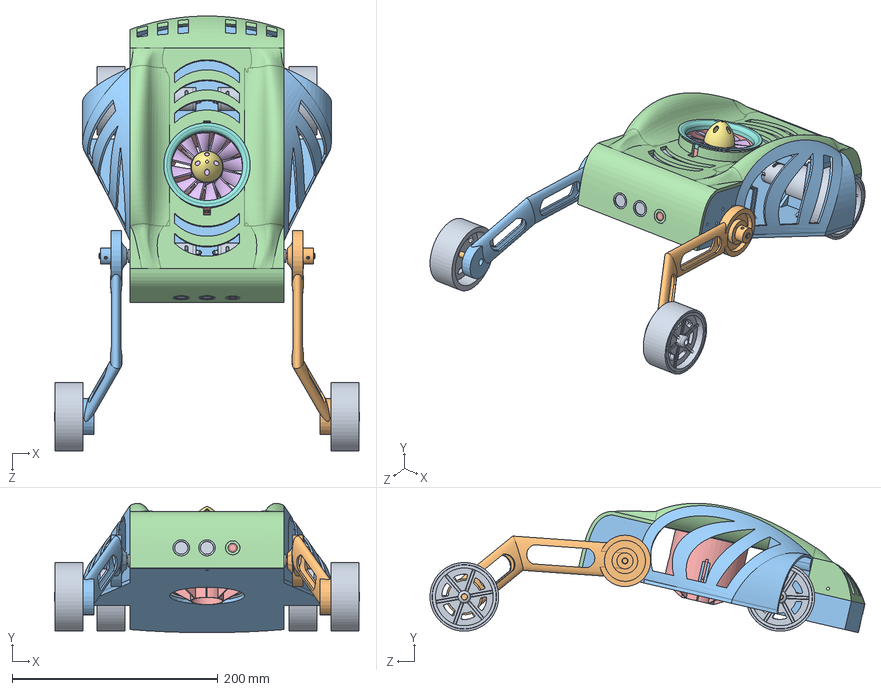
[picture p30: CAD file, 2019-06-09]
design/shadowBot.SLDASM
296.7 x 125.8 x 422.7 mm
wheel x 4
motorShaft x 5
chassis
surfacePlate
edf_housing
edf_blades
edf_wiresNose
edf_rim
urFinder
PCB 1
Camera Block
Camera end
Lenz
15 Pin Ribbon Block
Ribbon Clamp
0603 Resistor x 4
motor x 4
leftArm
rightArm

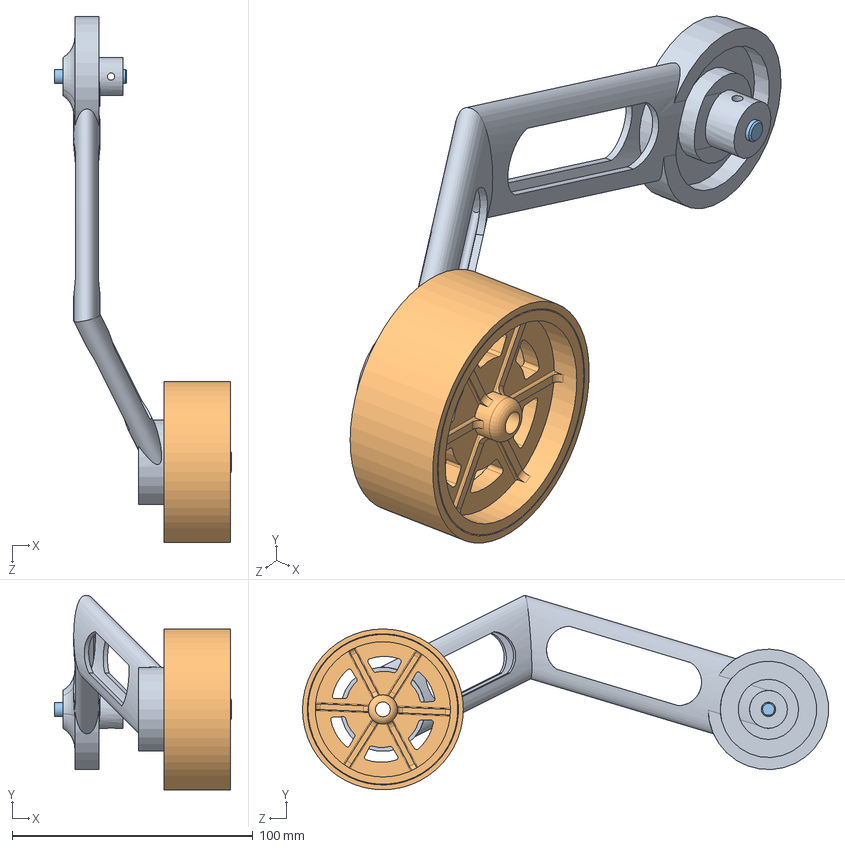
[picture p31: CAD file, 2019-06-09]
design/parts/leftArmWheel.SLDASM
73.5 x 80.7 x 218.3 mm
leftArm
wheel
motorShaft

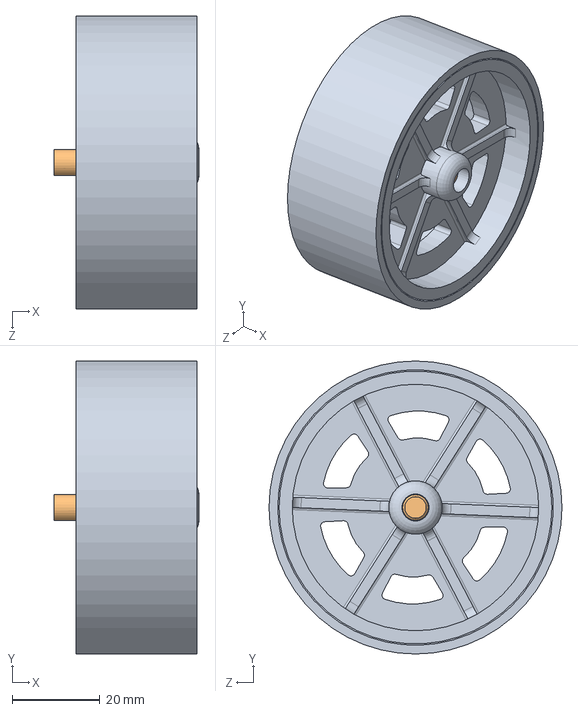
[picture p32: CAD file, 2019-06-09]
design/parts/shaftWheel.SLDASM
33.0 x 66.7 x 66.7 mm
wheel
motorShaft

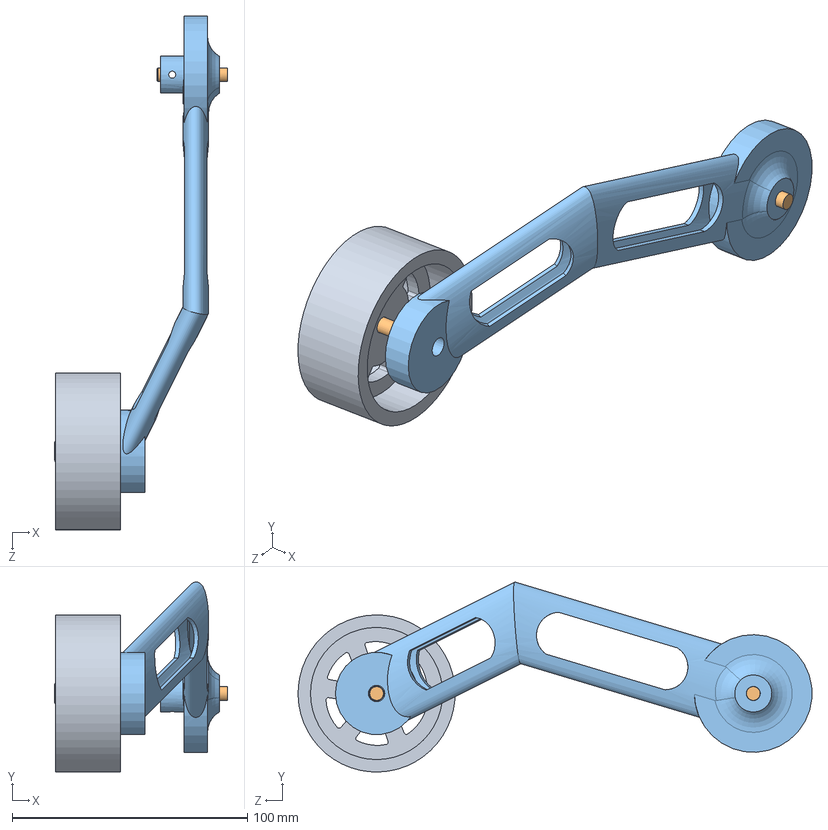
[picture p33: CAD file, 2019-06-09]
design/parts/rightArmWheel.SLDASM
73.5 x 80.7 x 218.3 mm
wheel
motorShaft x 2
rightArm

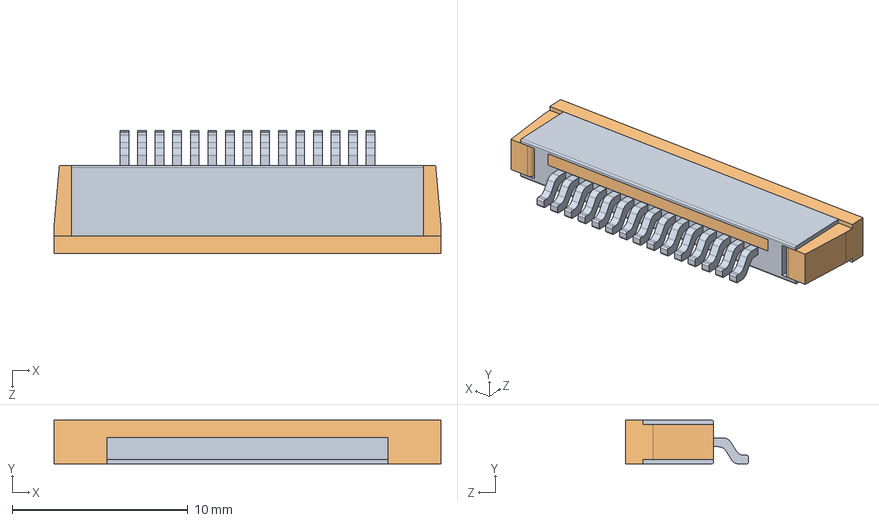
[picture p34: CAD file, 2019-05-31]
design/parts/piCam/15 Pin Ribbon Block Assem.SLDASM
22.0 x 2.50 x 7.00 mm
15 Pin Ribbon Block
Ribbon Clamp

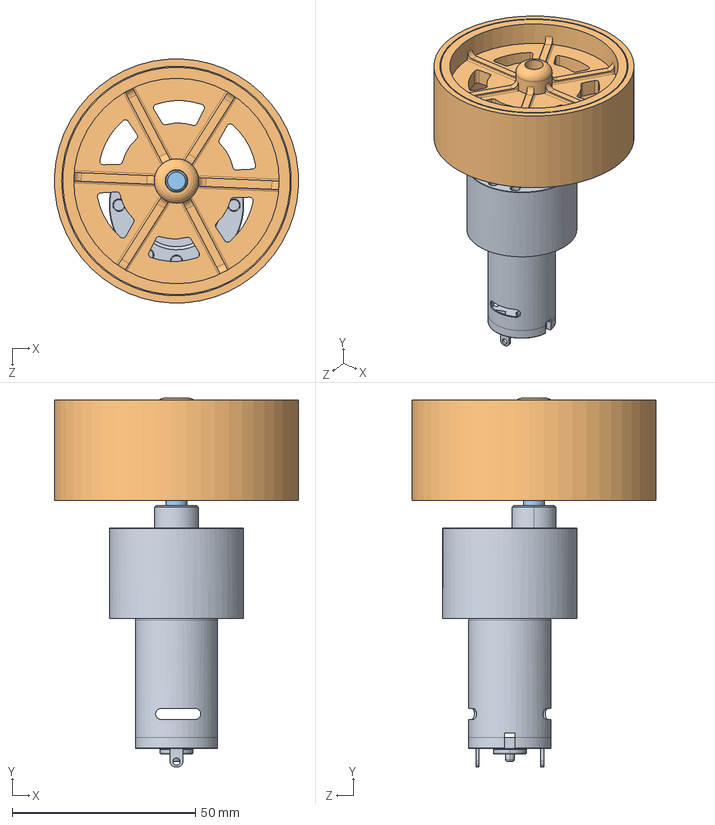
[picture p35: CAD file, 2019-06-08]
design/parts/motorWheel.SLDASM
66.7 x 100.8 x 66.7 mm
motor
wheel
motorShaft

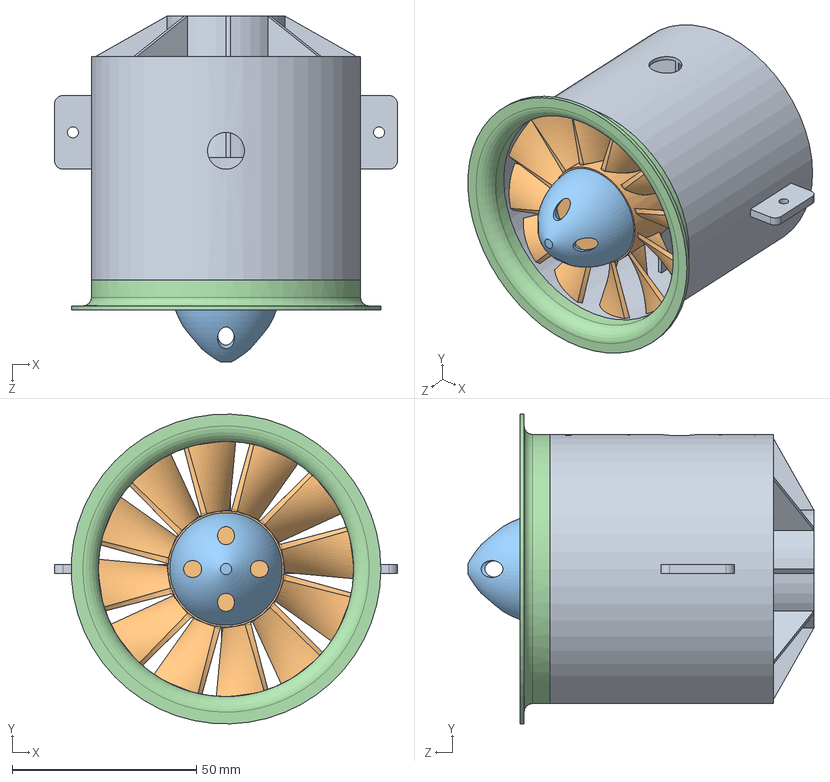
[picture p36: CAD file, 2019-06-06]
design/parts/edf.SLDASM
93.0 x 84.0 x 93.7 mm
edf_housing
edf_blades
edf_wiresNose
edf_rim

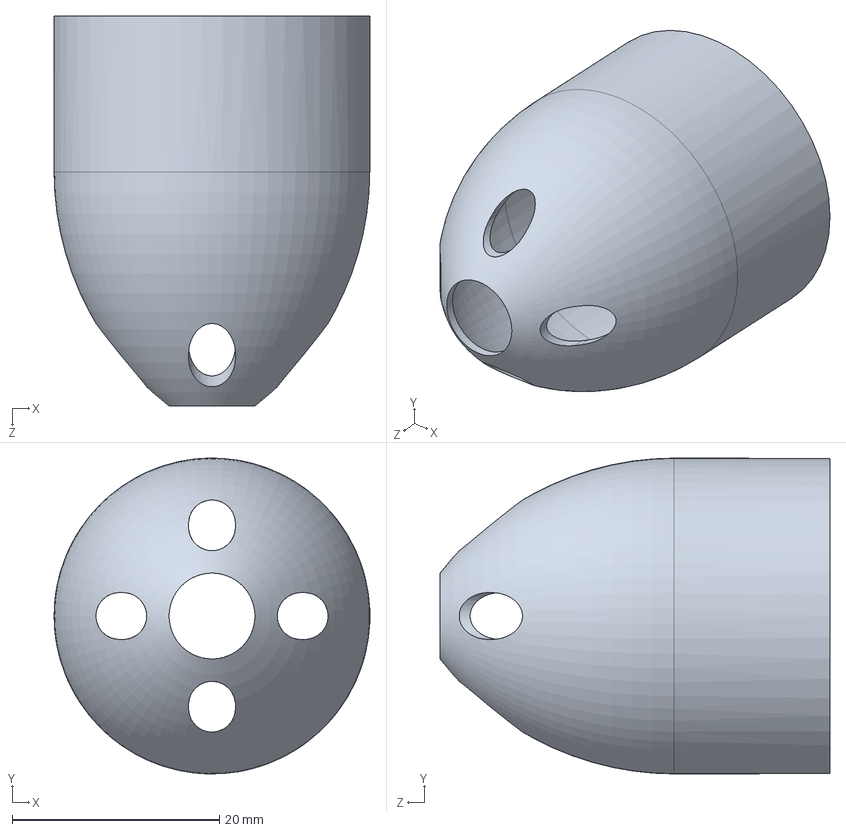
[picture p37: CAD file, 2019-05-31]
design/parts/edf/edf_nose.SLDPRT
30.5 x 30.5 x 37.7 mm

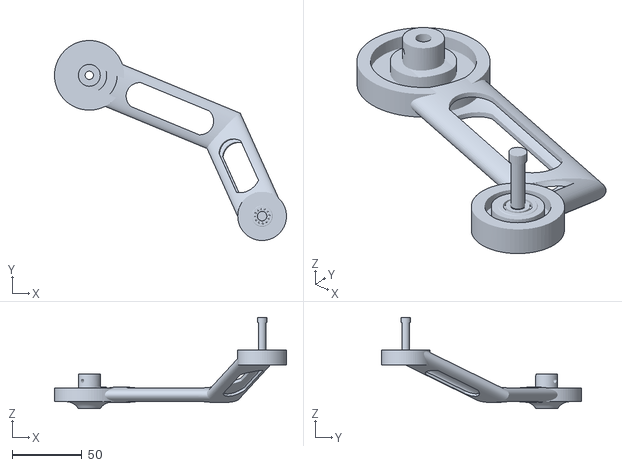
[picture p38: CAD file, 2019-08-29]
design/stl/gazebo-stl/right-links.stl
166.5 x 143.6 x 65.6

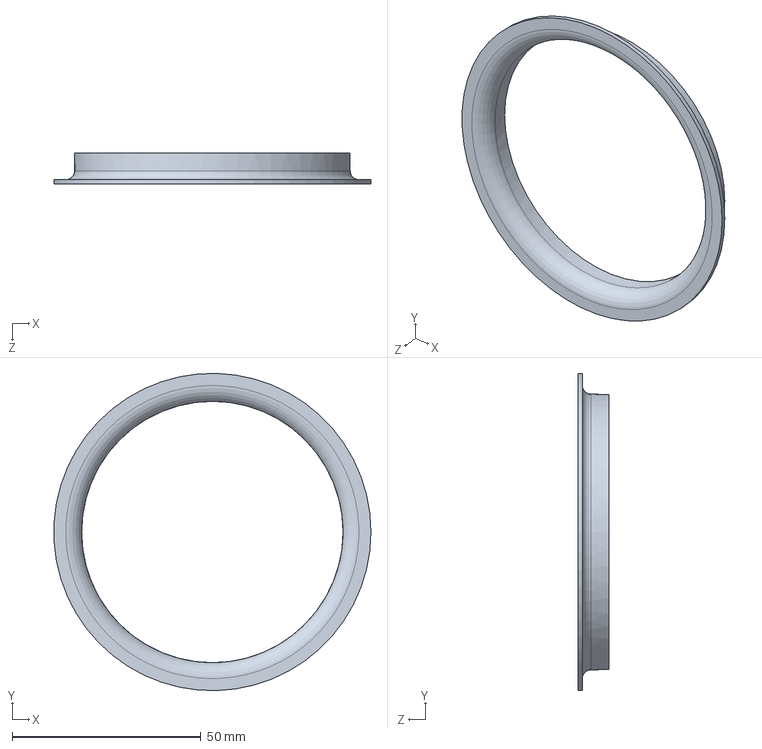
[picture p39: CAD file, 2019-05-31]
design/parts/edf/edf_rim.SLDPRT
83.9 x 84.0 x 8.18 mm

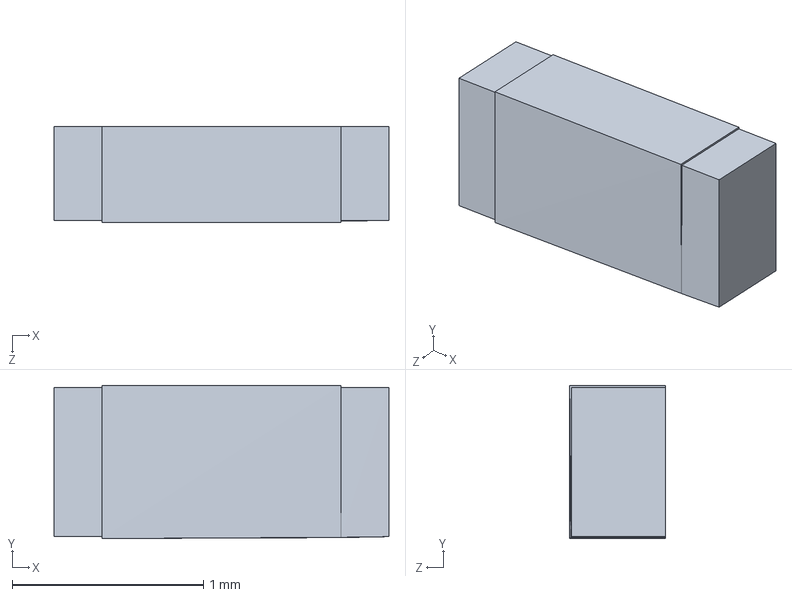
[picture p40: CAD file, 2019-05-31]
design/parts/piCam/0603 Resistor.SLDPRT
1.75 x 0.8 x 0.5 mm

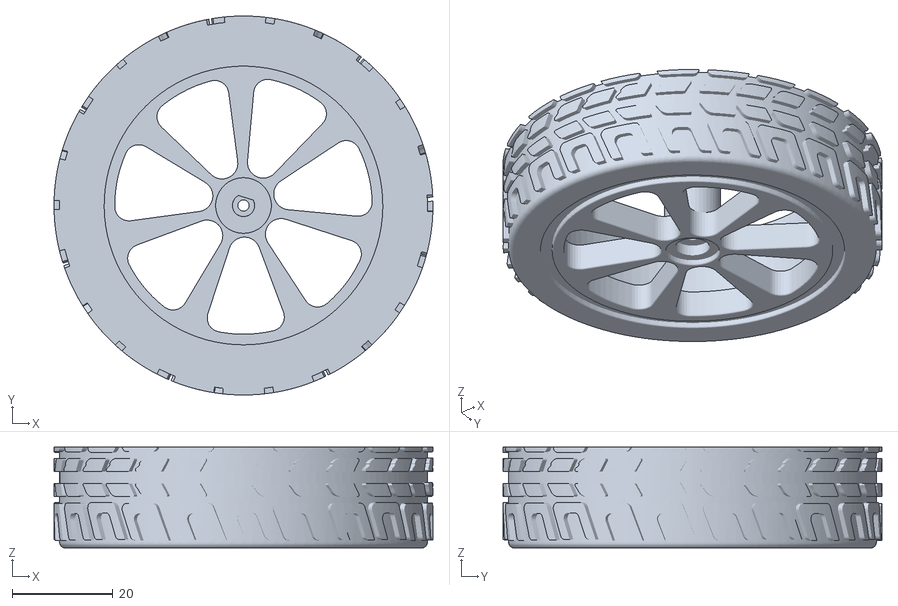
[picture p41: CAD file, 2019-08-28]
design/stl/gazebo-stl/front-wheel.stl
75.1 x 75.1 x 20.0

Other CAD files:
design/parts/edf/edf_wiresNose.SLDPRT
design/parts/piCam/Ribbon Clamp.SLDPRT
design/stl/gazebo-stl/left-links.stl
design/parts/edf/edf_motor.SLDPRT
design/inventor-design/0603 Resistor.ipt
design/inventor-design/15 Pin Ribbon Block Assem.iam
design/inventor-design/330KV Top Assembly v3.iam
design/inventor-design/5972K91(Mirror) (1).ipt
design/inventor-design/628_6-2Z.iam
design/inventor-design/628_6-2Z_1.iam
design/inventor-design/628_6-2Z_PART1.ipt
design/inventor-design/628_6-2Z_PART2.ipt
design/inventor-design/628_6-2Z_PART3.ipt
design/inventor-design/628_6-2Z_PART4.ipt
design/inventor-design/628_6-2Z_PART5.ipt
design/inventor-design/Camera Block.ipt
design/inventor-design/Camera Module Assem v1.iam
design/inventor-design/Camera end.ipt
design/inventor-design/Iron Core.ipt
design/inventor-design/Lenz.ipt
design/inventor-design/Magnet.ipt
design/inventor-design/Outer Casing.ipt
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

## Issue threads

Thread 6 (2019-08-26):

Rear wheels are floating!

imsenthur, 2019-08-26:
[bot-isometric](https://github.com/spider-tronix/shadow-bot/blob/master/design/renders/bot-isometric.jpg)
[bot-side-view](https://github.com/spider-tronix/shadow-bot/blob/master/design/renders/bot-side-view.jpg)

Kindly fix this @jaxxstar.

Closed 2019-09-04.

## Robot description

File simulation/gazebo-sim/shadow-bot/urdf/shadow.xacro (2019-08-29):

<?xml version="1.0"?>
<robot name="differential_wheeled_robot" xmlns:xacro="http://www.ros.org/wiki/xacro">
  

  <xacro:include filename="$(find shadow-bot)/urdf/wheel.urdf.xacro" /> 

  <material name="Black">
    <color rgba="0.0 0.0 0.0 1.0"/>
  </material>

  <material name="Red">
    <color rgba="0.8 0.0 0.0 1.0"/>
  </material>

  <material name="White">
    <color rgba="1.0 1.0 1.0 1.0"/>
  </material>

  <material name="Blue">
    <color rgba="0.0 0.0 0.8 1.0"/>
  </material>

  <property name="M_PI" value="3.1415926535897931" />
  <property name="M_PI_2" value="1.570796327" />
  <property name="DEG_TO_RAD" value="0.017453293" />

  <!-- body -->
  <property name="base_mass" value="2.5" /> 

  <!-- arm -->
  <property name="arm_mass" value="1.0" /> 

  <!-- wheels -->
  <property name="wheel_mass" value="0.2" /> 
  
  <property name="base_x_origin_to_wheel_origin" value="-0.110" />
  <property name="base_y_origin_to_wheel_origin" value="0.095" />
  <property name="base_z_origin_to_wheel_origin" value="-0.005" />

  <property name="arm_x_origin_to_wheel_origin" value="0.160" />
  <property name="arm_y_origin_to_wheel_origin" value="-0.045" />
  <property name="arm_z_origin_to_wheel_origin" value="0.0" />

  <!-- inertia -->
  <macro name="cylinder_inertia" params="m r h">
    <inertia ixx="${m*(3*r*r+h*h)/12}" ixy = "0" ixz = "0" iyy="${m*(3*r*r+h*h)/12}" iyz = "0" izz="${m*r*r/2}" /> 
  </macro>

  <macro name="box_inertia" params="m x y z">
    <inertia ixx="${m*(y*y+z*z)/12}" ixy = "0" ixz = "0" iyy="${m*(x*x+z*z)/12}" iyz = "0" izz="${m*(x*x+y*y)/12}" /> 
  </macro>

  <gazebo>
    <plugin name="gazebo_ros_control" filename="libgazebo_ros_control.so">
    </plugin>
  </gazebo>

 <link name="base_footprint">
    <visual>
        <origin xyz="0 0 0" rpy="0 0 0" />
        <geometry>
            <box size="0.001 0.001 0.001" />
        </geometry>
    </visual>
  </link>

  <gazebo reference="base_footprint">
    <turnGravityOff>false</turnGravityOff>
  </gazebo>

  <joint name="base_footprint_joint" type="fixed">
    <origin xyz="0 0 ${wheel_radius - base_z_origin_to_wheel_origin}" rpy="0 0 0" />
    <parent link="base_footprint"/>
    <child link="base_link" />
  </joint>

  <link name="base_link">
    <inertial>
      <mass value="${base_mass}" />
      <origin xyz="0 0 0" />
      <!--The 3x3 rotational inertia matrix. -->
        <box_inertia m="${base_mass}" x="0.262" y="0.150" z="0.06" />

    </inertial>    
    <visual>
      <origin xyz="0.003 0 0.0065" rpy="0 0 ${M_PI/2}" />
      <geometry>
        <mesh filename="package://shadow-bot/meshes/dae/chassis.dae"/>
      </geometry>
      <material name="White" />
    </visual>  
    <collision>
      <origin xyz="0 0 0" rpy="0 0 0 " />
      <geometry>
          <box size="0.262 0.150 0.06" />
      </geometry>
    </collision>     
  </link>
  <gazebo reference="base_link">
    <material>Gazebo/White</material>
    <turnGravityOff>false</turnGravityOff>
  </gazebo>

  <link name="left_arm">
    <inertial>
      <mass value="${arm_mass}" />
      <origin xyz="0.085 0 0" rpy="0 0 0" />
      <!--The 3x3 rotational inertia matrix. -->
        <box_inertia m="${arm_mass}" x="0.170" y="0.015" z="0.025" />
    </inertial>    

    <visual>
      <origin xyz="0.0625 0.02 0.0115" rpy="${-M_PI/5} 0 ${M_PI/2}" />
      <geometry>
        <mesh filename="package://shadow-bot/meshes/dae/left-arm.dae"/>
      </geometry>
      <material name="White" />
    </visual>  
    <collision>
      <origin xyz="0.085 0 0" rpy="0 0 0 " />
      <geometry>
          <box size="0.170 0.015 0.025" />
      </geometry>
    </collision>     
  </link>
  <gazebo reference="left_link">
    <material>Gazebo/White</material>
    <turnGravityOff>false</turnGravityOff>
  </gazebo>
  
  <joint name="left_arm_joint" type="revolute">
    <parent link="base_link"/>
    <child link="left_arm"/>
    <origin xyz="0.0930 0.09 -0.0135" rpy="0 0 0" />
    <axis xyz="0 1 0"/>
    <dynamics damping="0.0" friction="0.0"/>
    <limit effort="1000.0" lower="${-5*M_PI/12}" upper="${5*M_PI/12}" velocity="1000.0"/>
  </joint>

  <transmission name="left_arm_joint_trans">
    <type>transmission_interface/SimpleTransmission</type>
    <joint name="left_arm_joint">
      <hardwareInterface>hardware_interface/PositionJointInterface</hardwareInterface>
    </joint>
    <actuator name="left_arm_joint_motor">
      <hardwareInterface>hardware_interface/PositionJointInterface</hardwareInterface>
      <mechanicalReduction>10</mechanicalReduction>
    </actuator>
  </transmission>


  <link name="right_arm">
    <inertial>
      <mass value="${arm_mass}" />
      <origin xyz="0.085 0 0" rpy="0 0 0" />
      <!--The 3x3 rotational inertia matrix. -->
        <box_inertia m="${arm_mass}" x="0.170" y="0.015" z="0.025" />
    </inertial>    
    <visual>
      <origin xyz="0.0625 -0.02 0.0115" rpy="${-M_PI/5} 0 ${M_PI/2}" />
      <geometry>
        <mesh filename="package://shadow-bot/meshes/dae/right-arm.dae"/>
      </geometry>
      <material name="White" />
    </visual>  
    <collision>
      <origin xyz="0.085 0 0" rpy="0 0 0 " />
      <geometry>
          <box size="0.170 0.015 0.025" />
      </geometry>
    </collision>     
  </link>
  <gazebo reference="right_link">
    <material>Gazebo/White</material>
    <turnGravityOff>false</turnGravityOff>
  </gazebo>
  
  <joint name="right_arm_joint" type="revolute">
    <parent link="base_link"/>
    <child link="right_arm"/>
    <origin xyz="0.0930 -0.09 -0.0135" rpy="0 0 0" />
    <axis xyz="0 1 0"/>
    <dynamics damping="0.0" friction="0.0"/>
    <limit effort="1000.0" lower="${-5*M_PI/12}" upper="${5*M_PI/12}" velocity="1000.0"/>
  </joint>

  <transmission name="right_arm_joint_trans">
    <type>transmission_interface/SimpleTransmission</type>
    <joint name="right_arm_joint">
      <hardwareInterface>hardware_interface/PositionJointInterface</hardwareInterface>
    </joint>
    <actuator name="right_arm_joint_motor">
      <hardwareInterface>hardware_interface/PositionJointInterface</hardwareInterface>
      <mechanicalReduction>10</mechanicalReduction>
    </actuator>
  </transmission>


<!-- Wheel Definitions -->

  <wheel fb="front" lr="right" parent="base_link" translateX="${base_x_origin_to_wheel_origin}" translateY="${base_y_origin_to_wheel_origin}" translateZ="${base_z_origin_to_wheel_origin}" flipY="1"/>
  <wheel fb="front" lr="left" parent="base_link" translateX="${base_x_origin_to_wheel_origin}" translateY="-${base_y_origin_to_wheel_origin}" translateZ="${base_z_origin_to_wheel_origin}" flipY="-1"/>
	   
  <arm_wheel fb="arm" lr="right" parent="right_arm" translateX="${arm_x_origin_to_wheel_origin}" translateY="${arm_y_origin_to_wheel_origin}" translateZ="${arm_z_origin_to_wheel_origin}" flipY="1"/>
  <arm_wheel fb="arm" lr="left" parent="left_arm" translateX="${arm_x_origin_to_wheel_origin}" translateY="${-1 * arm_y_origin_to_wheel_origin}" translateZ="${arm_z_origin_to_wheel_origin}" flipY="-1"/>
	   
  <!-- Differential drive controller  -->
  <gazebo>
    <plugin name="differential_drive_controller" filename="libgazebo_ros_diff_drive.so">
      <rosDebugLevel>Debug</rosDebugLevel>
      <publishWheelTF>false</publishWheelTF>
      <robotNamespace>/</robotNamespace>
      <publishTf>1</publishTf>
      <publishWheelJointState>false</publishWheelJointState>
      <alwaysOn>true</alwaysOn>
      <updateRate>100.0</updateRate>
      <leftJoint>front_left_wheel_joint</leftJoint>
      <rightJoint>front_right_wheel_joint</rightJoint>
      <wheelSeparation>0.150</wheelSeparation>
      <wheelDiameter>${2*wheel_radius}</wheelDiameter>
      <broadcastTF>1</broadcastTF>
      <wheelTorque>40</wheelTorque>
      <wheelAcceleration>1.8</wheelAcceleration>
      <commandTopic>cmd_vel</commandTopic>
      <odometryFrame>odom</odometryFrame> 
      <odometryTopic>odom</odometryTopic> 
      <robotBaseFrame>base_footprint</robotBaseFrame>
    </plugin>
  </gazebo> 
</robot>

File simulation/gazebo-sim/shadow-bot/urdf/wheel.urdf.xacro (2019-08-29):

<?xml version="1.0"?>
<robot name="wheel" xmlns:xacro="http://www.ros.org/wiki/xacro">
  
  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
  <property name="wheel_radius" value="0.050" /> 
  <property name="arm_wheel_radius" value="0.0350" /> 
  <property name="wheel_height" value="0.02" />
  <property name="arm_wheel_height" value="0.025" />
  <property name="wheel_mass" value="0.15" /> 
  <property name="arm_wheel_mass" value="0.005" /> 
  
  <property name="base_x_origin_to_wheel_origin" value="-0.110" />
  <property name="base_y_origin_to_wheel_origin" value="0.095" />
  <property name="base_z_origin_to_wheel_origin" value="-0.005" />
  
  <macro name="cylinder_inertia" params="m r h">
    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 
  </macro>
  
  <xacro:macro name="wheel" params="fb lr parent translateX translateY translateZ flipY"> 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
    <link name="${fb}_${lr}_wheel">
      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
      <inertial>
        <mass value="${wheel_mass}" />
        <origin xyz="0 0 0" rpy="${flipY*M_PI/2} 0 0 " />
        <cylinder_inertia m="${wheel_mass}" r="${wheel_radius}" h="${wheel_height}" />
      </inertial>
    </link>

    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

    <joint name="${fb}_${lr}_wheel_joint" type="continuous">
      <parent link="${parent}"/>
      <child link="${fb}_${lr}_wheel"/>
      <origin xyz="${translateX} ${translateY} ${translateZ}" rpy="0 0 0" /> 
      <axis xyz="0 1 0" rpy="0 0" />
      <limit effort="100" velocity="100"/>
      <joint_properties damping="0.5" friction="100.0"/>
    </joint>

    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
   
  </xacro:macro>

    <xacro:macro name="arm_wheel" params="fb lr parent translateX translateY translateZ flipY"> 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
    <link name="${fb}_${lr}_wheel">
      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
      <inertial>
        <mass value="${arm_wheel_mass}" />
        <origin xyz="0 0 0" rpy="${flipY*M_PI/2} 0 0 " />
        <cylinder_inertia m="${arm_wheel_mass}" r="${arm_wheel_radius}" h="${arm_wheel_height}" />
      </inertial>
    </link>

    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

    <joint name="${fb}_${lr}_wheel_joint" type="continuous">
      <parent link="${parent}"/>
      <child link="${fb}_${lr}_wheel"/>
      <origin xyz="${translateX} ${translateY} ${translateZ}" rpy="0 0 0" /> 
      <axis xyz="0 1 0" rpy="0 0" />
      <limit effort="10000" velocity="10000"/>
      <joint_properties damping="0.0" friction="0.0"/>
    </joint>

    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
   
  </xacro:macro>
</robot>

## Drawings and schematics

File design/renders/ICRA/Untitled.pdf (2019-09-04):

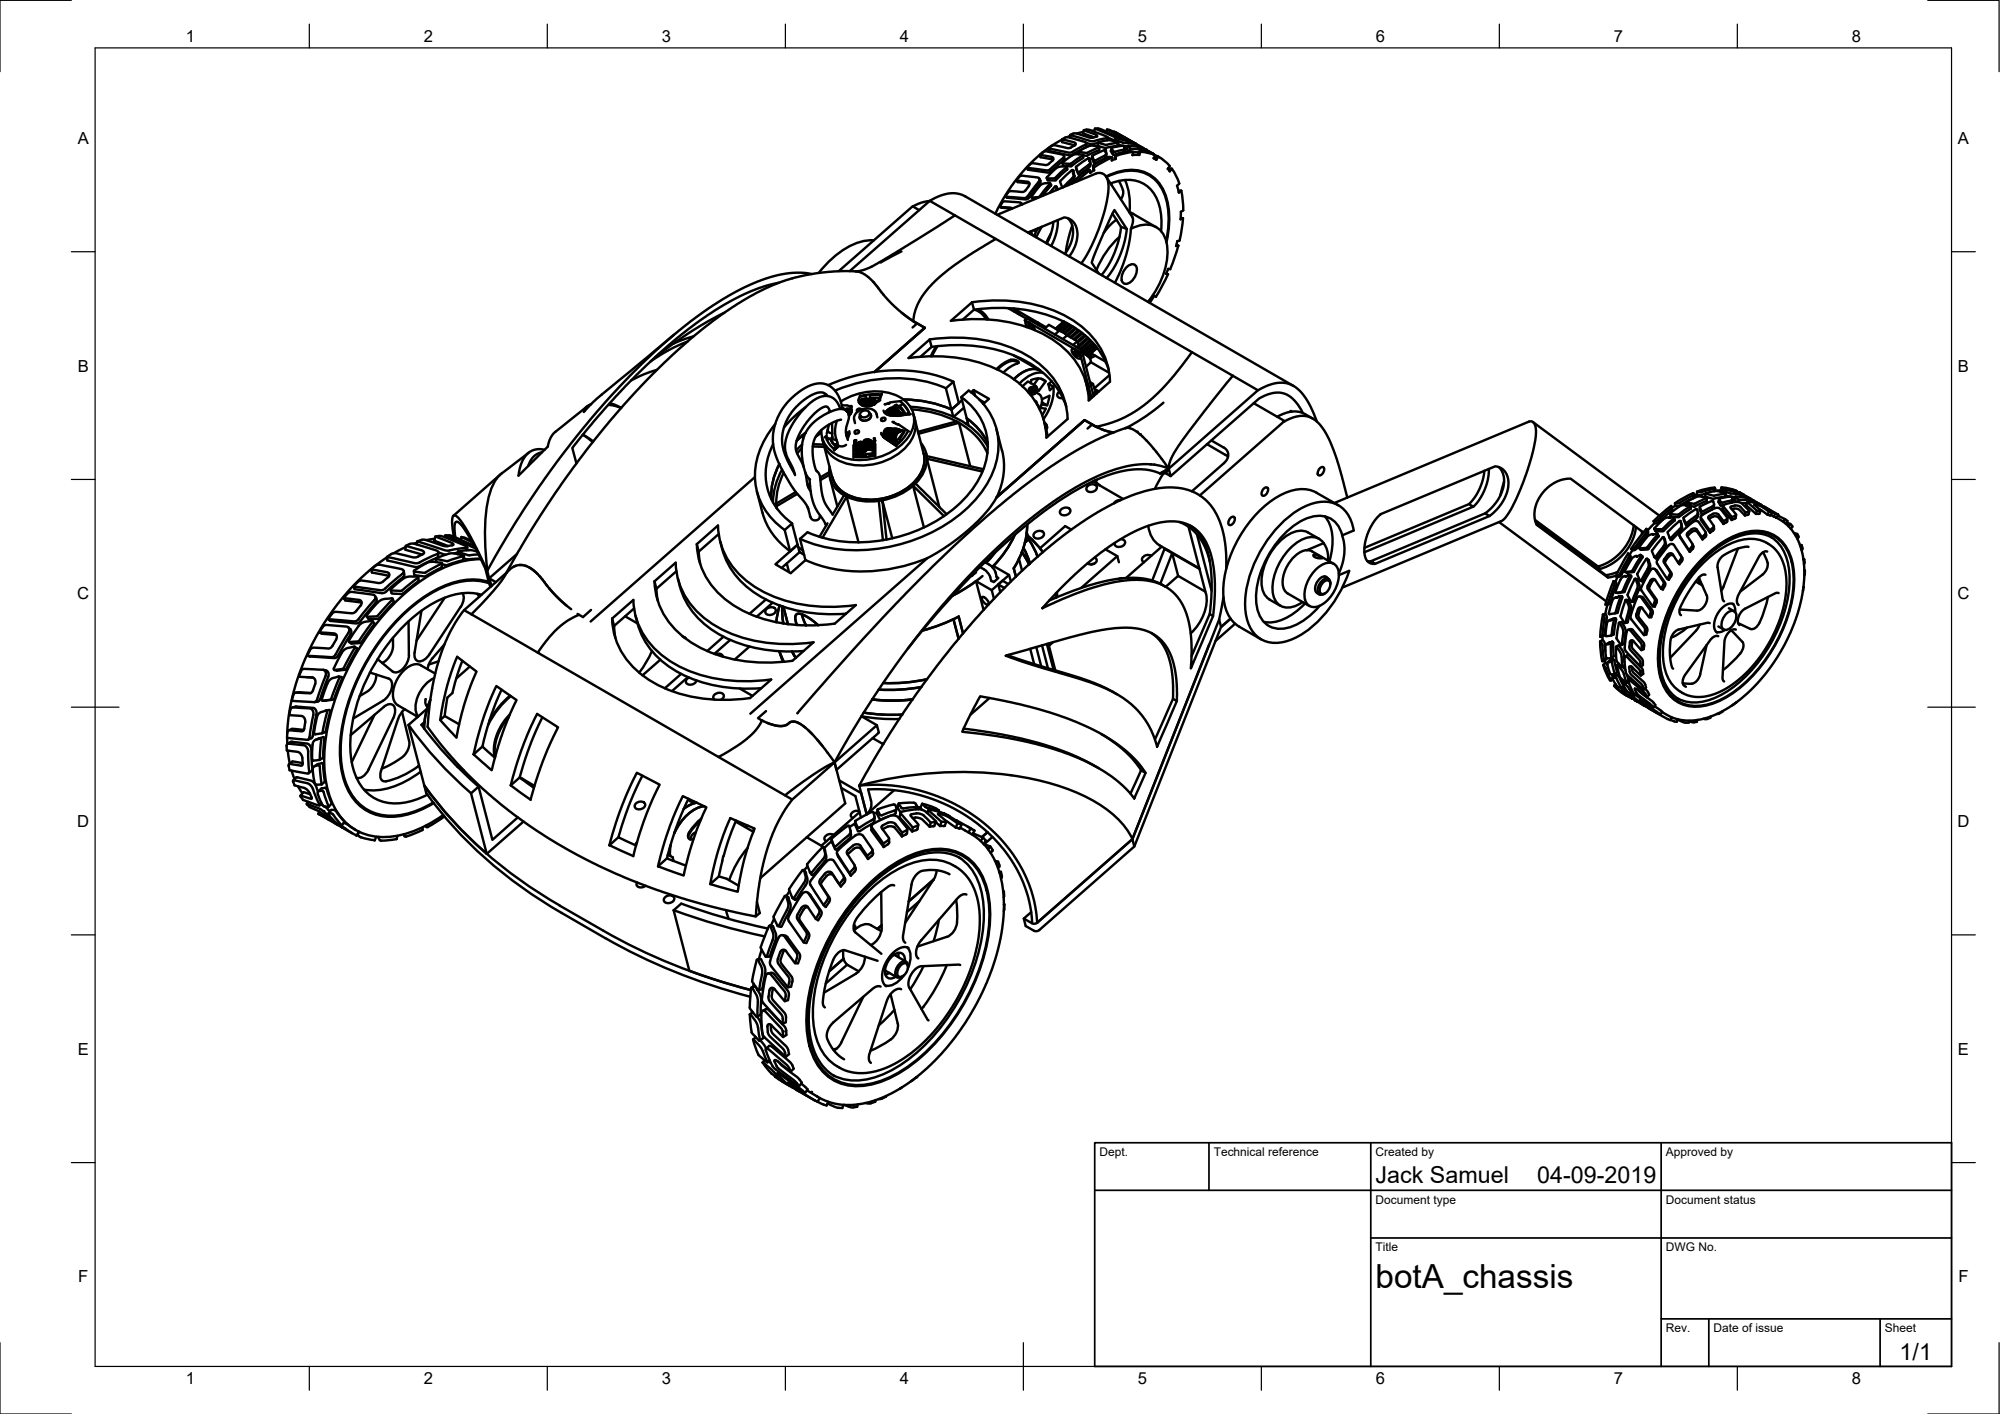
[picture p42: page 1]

Dept. | Technical reference | Created by Jack Samuel 04-09-2019 | Approved by

Document type | Document status

Title botA_chassis | DWG No.

Rev. | Date of issue | Sheet 1/1

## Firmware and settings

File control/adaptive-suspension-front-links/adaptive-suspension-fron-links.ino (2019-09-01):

#include <PID_v1.h>  //Left motor header
//--------------- ENCODER PINS/VARIABLES FOR LEFT -----------------//

#define encoderPinLA 2
#define encoderPinLB 4
int PPR = 4920;  // Encoder Pulse per revolution.
int angle = 360; // Maximum degree of motion.
int left_aState;
int left_counter;

//--------------- ENCODER PINS/VARIABLES FOR RIGHT -----------------//

#define encoderPinRinterrupt 1
#define encoderPinRA 3
#define encoderPinRB 7
//int PPR = 4920;  // Encoder Pulse per revolution.
//int angle = 360; // Maximum degree of motion.
int right_aState;
int right_counter;

//---------------- MOTOR PINS/VARIABLES FOR LEFT ------------------//

#define LEnable 17 //Motor Enamble pin Runs on PWM signal
#define LFwd  19  // Motor Forward pin
#define LRev  18 // Motor Reverse pin
int User_InputL = 30;  // left Positive angle is down
int REVL = 0;
int linkanglel = 0;

//---------------- MOTOR PINS/VARIABLES FOR RIGHT ------------------//

#define REnable 16 //Motor Enamble pin Runs on PWM signal
#define RFwd  14   // Motor Forward pin
#define RRev  15   // Motor Reverse pin
int User_InputR = 0;
int REVR = 0;
int linkangler = 0;

//------------------- PID VARIABLES FOR RIGHT----------------------//
double error = 0;
double angleInp = 0; //make it NEGATIVE
double setpointR = 0;
double thetar = 0;
int overshootflagr = 0;
double errord = 0;
double preverror = 0;
double errori = 0;
double controlinput = 0;
double dt = 0;

double kpr = .2, kir = 0, kdr = 0/10000; // modify for optimal performance
double inputr = 0, outputr = 0, setpointr = 0;


//------------------- PID VARIABLES FOR LEFT ----------------------//

//IF THE MOTOR DRIVER HEATS UP, THE MOTORS GO CRAZY
//TO BE FINE TUNED
int i = 45; //Link angles

double kpl = .04, kil = 0.0, kdl = 0/10000; // modify for optimal performance
double inputl = 0, outputl = 0, setpointl = 0;
double thetal = 0;
int overshootflagl = 0;

PID myPIDL(&inputl, &outputl, &setpointl, kpl, kil, kdl, DIRECT);

//------------------- MODIFIED DYNAMICS CHART ----------------------//
/* ================================================================= /
 *  SPRING 1 => double kpl = 0.35, kil = 0, kdl = 0 /10000;
 *  SPRING 2 => double kpl = 0.65, kil = 0, kdl = 0 /10000;
 *  DAMPER 1 => double kpl = 0.65, kil = 0, kdl = 2 /10000;
 *  DAMPER 2 => double kpl = 0.65, kil = 0, kdl = 6 /10000;
   ================================================================ */
//------------------------------------------------------------------//

void setup() 
{
  motorSetupL();
  motorSetupR();
  Serial.begin(9600); //initialize serial comunication
  encoderSetupL();      //Serial communication is messing with the timers and analog pin output
  encoderSetupR();
  

  //--------- Timer setup ----------//
  TCCR1B = TCCR1B & 0b11111000 | 1;
  
  myPIDL.SetMode(AUTOMATIC);          //set PID in Auto mode
  myPIDL.SetSampleTime(1);            //refresh rate of PID controller
  myPIDL.SetOutputLimits(-255, 255);  //this is the MAX PWM value to move motor, here change in value reflect change in speed of motor.
   //--------- Timer setup ----------//
  TCCR1B = TCCR1B & 0b11111000 | 1;
  //analogWrite(REnable,0);
 
}

void loop() 
{

  angleInp = -90;     //right, negative here is downward in bot
  User_InputL = 60;   //left, positive here is downward in bot
  
  REVL = remapl(User_InputL);
  setpointl = REVL;
  inputl = left_counter;
  linkanglel = (left_counter*0.073170732); // To print left link angle if reqd.
  linkanglel = linkanglel%360;
 
  
  myPIDL.Compute();
  pwmOutl(outputl);
  setpointR = angleInp;
  thetar = invRemap(right_counter);
  thetal = invRemap(left_counter);
  if (overshootflagl == 1)
  {
    //Serial.println("Left Cutoff");
    //finishl();
   // delay(100);
  }
  if (overshootflagr == 1)
  {
    //Serial.println("Right Cutoff");
   // finishr();
   // delay(100);
  }
  error = thetar - setpointR;
  errord = (error -preverror);
  errori += (error);
  controlinput = (kpr*error) + (kdr*errord) + (kir*errori);

  if(controlinput > 230)
  {
    controlinput = 230;
  }
  else if( controlinput < -230)
  {
    controlinput = -230;
  }
  
  if(controlinput < 150 && controlinput >10)
  {
    controlinput = 150;
  }
  else if( controlinput > -150 && controlinput < -10)
  {
    controlinput = -150;
  }
  if(controlinput > 230)
  {
    controlinput = 230;
  }
  else if( controlinput < -230)
  {
    controlinput = -230;
  }

  if (controlinput>=150)
  {
    forwardr();
    analogWrite(REnable,controlinput);
  }
  else if(controlinput <= -150)
  {
    reverser();
    analogWrite(REnable,abs(controlinput));
  }
  else 
  {
    finishr();
  }
 
  preverror = error;
}

void motorSetupL()
{
  pinMode(LEnable, OUTPUT);
  pinMode(LFwd, OUTPUT); 
  pinMode(LRev, OUTPUT);
}
void motorSetupR()
{
  pinMode(REnable, OUTPUT);
  pinMode(RFwd, OUTPUT); 
  pinMode(RRev, OUTPUT);
}

void encoderSetupL()
{
  pinMode(encoderPinLA, INPUT_PULLUP); 
  pinMode(encoderPinLB, INPUT_PULLUP);
  digitalWrite(encoderPinLA, HIGH); //turn pullup resistor on
  digitalWrite(encoderPinLB, HIGH); //turn pullup resistor on
  attachInterrupt(0, updateLEncoder, CHANGE); 
}
void encoderSetupR()
{
  pinMode(encoderPinRA, INPUT_PULLUP); 
  pinMode(encoderPinRB, INPUT_PULLUP);
  digitalWrite(encoderPinRA, HIGH); //turn pullup resistor on
  digitalWrite(encoderPinRB, HIGH); //turn pullup resistor on
  attachInterrupt(encoderPinRinterrupt, updateREncoder, CHANGE); 
}

void updateLEncoder()
{
  left_aState = digitalRead(encoderPinLA); 
    
     if(digitalRead(encoderPinLB) != left_aState) 
     { 
       left_counter ++;
     } 
     else 
     {
       left_counter --;
     }
  if(thetal > 95 )
    overshootflagl = 1;
  else if(thetal < -90 )
    overshootflagl = 1;
  else
    overshootflagl = 0;
}

void updateREncoder()
{
  right_aState = digitalRead(encoderPinRA); 
    
     if(digitalRead(encoderPinRB) != right_aState) 
     { 
       right_counter ++;
     } 
     else 
     {
       right_counter --;
     }
  if(thetar > 90 )
    overshootflagr = 1;
  else if(thetar < -95 )
    overshootflagr = 1;     
  else
    overshootflagr = 0;
}

void pwmOutl(int controlinput) 
{
  if(controlinput > 230)
  {
    controlinput = 230;
  }
  else if( controlinput < -230)
  {
    controlinput = -230;
  }
  
  if(controlinput < 150 && controlinput >10)
  {
    controlinput = 150;
  }
  else if( controlinput > -150 && controlinput < -10)
  {
    controlinput = -150;
  }
  if (controlinput>=150)
  {
    forwardl();
    analogWrite(LEnable,controlinput);
  }
  else if(controlinput <= -150)
  {
    reversel();
    analogWrite(LEnable,abs(controlinput));
  }
  else 
  {
    finishl();
  }
  Serial.println(controlinput);

}

void forwardl () 
{
  digitalWrite(LFwd, HIGH); 
  digitalWrite(LRev, LOW); 
}

void reversel () 
{
  digitalWrite(LFwd, LOW); 
  digitalWrite(LRev, HIGH); 
}

void finishl () 
{
  digitalWrite(LFwd, LOW); 
  digitalWrite(LRev, LOW); 
}
void forwardr () 
{
  digitalWrite(RFwd, HIGH); 
  digitalWrite(RRev, LOW); 
}

void reverser () 
{
  digitalWrite(RFwd, LOW); 
  digitalWrite(RRev, HIGH); 
}

void finishr () 
{
  digitalWrite(RFwd, LOW); 
  digitalWrite(RRev, LOW); 
}

int remapl (int thetal)
{
  int pulsel = floor(13.667 * thetal);
  return pulsel;
}
int remapr (int thetar)
{
  // jack-proof
  int pulser = floor(13.667 * thetar);
  return pulser;
}
int invRemap(int counter)
{
  // jack-proof
  int angle = counter*0.073170732;
  linkangler = (angle%360);
  //Serial.println(linkangler);
  return linkangler;
}

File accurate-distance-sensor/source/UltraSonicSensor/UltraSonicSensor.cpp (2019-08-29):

#include "UltraSonicSensor.h"
#include <avr/io.h>

void UltraSonicSensor::setPin(Pin pin, bool value) {
    switch (pin.port) {
        case 'B':
            if (value)
                PORTB |= (1 << pin.pin);
            else 
                PORTB &= !(1 << pin.pin);

            break;
            
        case 'C':
            if (value)
                PORTC |= (1 << pin.pin);
            else 
                PORTC &= !(1 << pin.pin);

            break;
            
        case 'D':
            if (value)
                PORTD |= (1 << pin.pin);
            else 
                PORTD &= !(1 << pin.pin);

            break;
    }
}

bool UltraSonicSensor::readPin(Pin pin) {
    switch (pin.port) {
        case 'B':
            return PINB & (1 << pin.pin);
        case 'C':
            return PINC & (1 << pin.pin);
        case 'D':
            return PIND & (1 << pin.pin);
    }
}

void UltraSonicSensor::setPinMode(Pin pin, PinMode mode) {
    switch (pin.port) {
        case 'B':
            if (mode) 
                DDRB |= (1 << pin.pin);
            else 
                DDRB &= !(1 << pin.pin);

        case 'C':
            if (mode) 
                DDRC |= (1 << pin.pin);
            else 
                DDRC &= !(1 << pin.pin);

        case 'D':
            if (mode) 
                DDRD |= (1 << pin.pin);
            else 
                DDRD &= !(1 << pin.pin);
    }
}

UltraSonicSensor::UltraSonicSensor(Pin trigger) {
    triggerPin = trigger;
    echoPin = Pin('C', 2);

    setPinMode(triggerPin, output);
    setPinMode(echoPin, input);

    distance = 0;
    status = idle;
    timer2Overflows = 0;
}

void UltraSonicSensor::wait(unsigned long us) {
    status = waiting;
    TCCR2A = (1 << WGM21);
    TCNT2 = 0;
    OCR2A = us * 2;
    TIMSK2 = 0;
    TCCR2B = (1 << CS21); //prescalar: 8
    while (!(TIFR2 & (1 << OCF2A)));
    TCCR2B = 0;
}

void UltraSonicSensor::sendTriggerPulse() {
    setPin(triggerPin, false);
    wait (2);
    setPin(triggerPin, true);
    wait (10);
    setPin(triggerPin, false);

    timer2Overflows = 0;

    //start counting
    TCCR2A = (1 << WGM21);
    TIMSK2 = (1 << OCIE2A);
    OCR2A = 100 * 2;
    TCNT2 = 0;

    //set interrupt to rising edge
    EICRA = (1 << ISC00) | (1 << ISC01);
}

void UltraSonicSensor::timer2CompAHandler() {
    if (status == measuring)
        timer2Overflows ++;
}

void UltraSonicSensor::echoPinRisingEdgeHadler() {
    if (status == waiting) {
        status = measuring;
        
        //start measuring
        TCCR2B = (1 << CS21);

        //change the interrupt to falling edge
        EICRA = (1 << ISC01);
    }
    else if (status == measuring) {
        unsigned long time = timer2Overflows * 100l + TCNT2 / 2;
        float d = time / 58.0f; //approx 
        updateDistance(d);
        
        sendTriggerPulse();
    }
}

float UltraSonicSensor::getDistance() {
    return distance;
}

Pin::Pin() {
    port = 'D';
    pin = 0;
}

Pin::Pin(char Port, int Pin) {
    pin = Pin;
    port = Port;
}

void UltraSonicSensor::start() {
    EIMSK = (1 << INT0);
    sendTriggerPulse();
}

void UltraSonicSensor::stop() {
    TCCR2B = 0;
    status = idle;
}

void UltraSonicSensor::test() {
    Pin testPin = Pin('B', 5);
    setPinMode(testPin, output);
    setPin(testPin, false);
}

void UltraSonicSensor::updateDistance(float newDistance) {
    // update distance
    distance = newDistance;
}

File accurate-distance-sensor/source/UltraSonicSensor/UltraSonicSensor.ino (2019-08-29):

/*
    Tester code for UltraSonicSensor Class
 */
#include <avr/interrupt.h>
#include <avr/io.h>
#include "UltraSonicSensor.h"

//sensor at pin
UltraSonicSensor sensor = UltraSonicSensor(Pin('D', 0));

int main() {
    sei(); //enable global interrupts
    Serial.begin(9600);
    sensor.start();

    while (1) {
        //display the distance
        float d = sensor.getDistance();
        Serial.print(d);
        Serial.print('\n');
    }

    return 0;
}

ISR (TIMER2_COMPA_vect) {
    sensor.timer2CompAHandler();
}

ISR (INT0_vect) {
    sensor.echoPinRisingEdgeHadler();
}

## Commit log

2019-05-24 Basic research on spring damper of cars
    Basic research on spring damper of cars and the type of modelling methods that can be used
2019-05-24 Basic research on spring damper of cars
    Basic research on spring damper of cars and different types of modelling
    We need to decide on which approach we are going to take
2019-05-25 Basic research on spring damper of cars updated
    We need to decide on which approach we are goingt to take
2019-05-26 Design_Files Added
    [chassis.STL, leftArm.STL, rightArm.STL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]
2019-05-31 added .stl exports
    [chassis.STL, leftArm.STL, rightArm.STL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]
2019-05-31 added individual parts (.SLDPRT)
    [0603 Resistor.SLDPRT, 15 Pin Ribbon Block Assem.SLDASM, 15 Pin Ribbon Block.SLDPRT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]
2019-05-31 Shadow bot, assemble! (.SLDASM)
    [shadowBot.SLDASM]
2019-05-31 DC-motor torque control added.
2019-06-03 Added Th: externally(by interaction) applied torque to the model.
2019-06-04 Fixing broken assembly.
    [shadowBot.SLDASM]
2019-06-06 shadowBot assembled.
    [edf.SLDASM, leftArm.SLDPRT, leftArmWheel.SLDASM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]
2019-06-08 Fixed mates and broken links.
    [Camera Module Assem.SLDASM, chassis.SLDPRT, leftArm.SLDPRT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]
2019-06-09 Segregated body from the assembly and fixed ground plane.
    [body.SLDASM, leftArmWheel.SLDASM, rightArmWheel.SLDASM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]
2019-07-15 Trajectory Generation
    In this problem we try to generate trajectories based on cubic splines.The cubic splines require a set of way-points and a set of time stamps during which they have to be traversed through.The way-points are generated from path planning algorithms and the time stamps are to determined based on the physical limitations of acceleration and velocities of our bot.This trajectory generation aims to generate a set of optimal time intervals which helps us to construct the required cubic spline.Since the optimization problem here is highly convex and non linear in case of cubic splines,we employ a method called particle swarm optimization to help us achieve our objective.
2019-08-05 Added few more .stl exports
    [body.stl, edf.stl, leftArmWheel.stl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]
2019-08-08 Gazebo simulation added.
    [shadow.xacro, wheel.urdf.xacro]
2019-08-13 Simple 2D Suspension Kinematic model added
2019-08-15 longitudinal-kinematics excluding wheels.
2019-08-16 Arduino configuration added.
    [arduino-config.txt]
2019-08-16 Added motor(2) configuration.
2019-08-16 Update arduino-config.txt
    Updated Arduino config
    [arduino-config.txt]
2019-08-16 Longitudinal forward-kinematics added.
2019-08-21 Added arduino code for pos-control
2019-08-21 Back motor control added
2019-08-21 Front motor control added
2019-08-21 Pin config updated
    [motor-config-front.txt]
2019-08-25 Back encoder test code
2019-08-25 Motor config updated
2019-08-26 Added back motor speed control
2019-08-26 Updated motor config
2019-08-26 implement UltraSonicSensor class (untested)
2019-08-26 Renamed Joint position controllers.
    [shadow.xacro, wheel.urdf.xacro]
2019-08-26 Switched to position-controller.
    [shadow.xacro]
2019-08-27 Switched back to effort-controllers for differential-drive.
    [shadow.xacro, wheel.urdf.xacro]
2019-08-27 Implement basic ultrasonic sensor
2019-08-28 Bot body stl added
2019-08-28 Rear wheel stl added
    [rear-wheel.stl]
2019-08-28 Right links stl added
    [right-links.stl]
2019-08-28 Left links stl added
    [left-links.stl]
2019-08-28 Added front wheel stl
    [front-wheel.stl]
2019-08-29 Fixed Moment of Inertia!
    [shadow.xacro]
2019-08-29 Added COR and Friction to the wheels.
    [wheel.urdf.xacro]
2019-08-29 Added new .stl to gazebo_ws.
    [front-wheel.stl, left-links.stl, rear-wheel.stl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]
2019-08-29 Tested normal working of Ultrasonic Sensor
2019-08-29 Added new collada models to URDF.
    [shadow.xacro]
2019-08-29 Fixed SDF formatting issue!
    [wheel.urdf.xacro]
2019-08-29 Tuned visual offsets for the wheels.
    [wheel.urdf.xacro]
2019-08-29 Deleted irrelevant stl models
    [front-wheel.stl, left-links.stl, rear-wheel.stl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]
2019-08-29 Right links modified
    [right-links.stl]
2019-08-29 Bugs in the previous version of multiple speed code rectified
    [esc_multiple_speed.ino]
2019-09-01 Modified back encoder test
2019-09-01 Edited motor control
2019-09-01 autodesk inventor design file added
    [0603 Resistor.ipt, 15 Pin Ribbon Block Assem.iam, 330KV Top Assembly v3.iam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]
2019-09-04 Full bot stl added (Front links at 30*)
2019-09-04 Flow-simulation added
2019-09-04 Added 30 deg stl
2019-09-04 45 deg stl added
2019-09-04 60 degree stl added
2019-09-04 Orientation of stl
2019-09-04 75 degree stl added
2019-09-05 Switching to Xflow from Flow-design.
2019-09-08 Flow-analysis result added.
2019-09-09 Added matlab cdX-plots.
    [15cdx.csv, 30cdx.csv, 45cdx.csv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]
2019-09-11 Changed new motor drivers and modified pin config
    [motor-config-front.txt]
2019-09-12 Modified flow-lines with theta value.
2019-09-12 Added transition-kinematics.
2019-09-12 Merged fdb and kinematics!
2019-09-13 Rectified new motor driver pin config
2019-09-14 added csv files
    [1-clean-log.csv, 2-clean-log.csv, 3-clean-log.csv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]
2019-09-17 Contact force variation with Thrust code added
2019-09-17 Contact force variation with thrust plot added
2019-09-19 Impedance control and esc pot control added
2019-09-19 Max V_A varying thrust code added
2019-09-19 Max V_A variation with thrust code added
2019-09-19 Max V_A variation for thrust with title image added
2019-09-19 Impedance Plot X axis range 0.6s added
2019-09-19 Normal force vs thrust plot added
2019-09-19 Nfr variation with thrust plot added
2019-09-19 Nfr variation with thrust with legend adjustment plot added
2019-09-19 Max V_A by varying thrust plot added
2019-09-19 Max V_A by varying thrust final plot added
2019-09-19 Opencv code to relay image to laptop added
